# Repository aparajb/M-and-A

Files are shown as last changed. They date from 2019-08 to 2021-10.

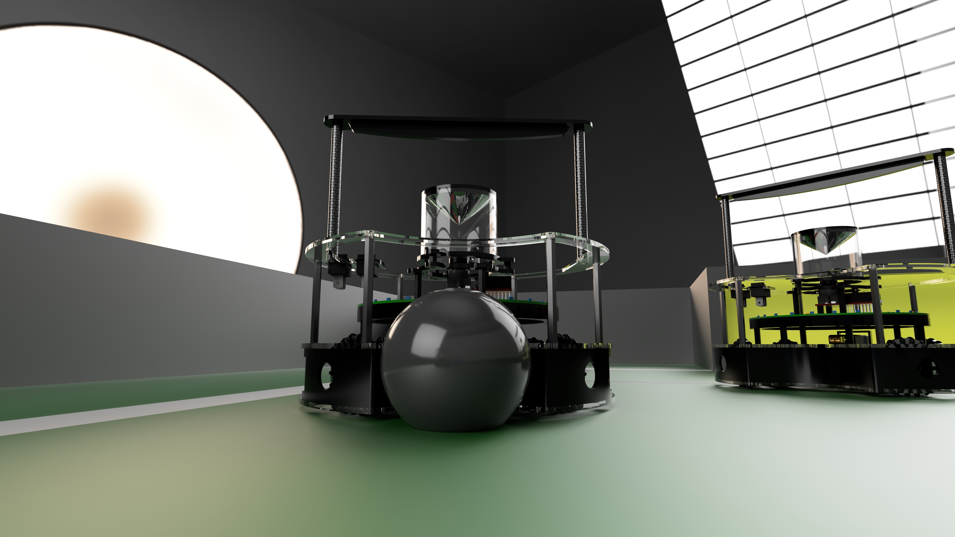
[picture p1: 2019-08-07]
M&A 2019/Hardware/Renders/Game Render 2.jpg

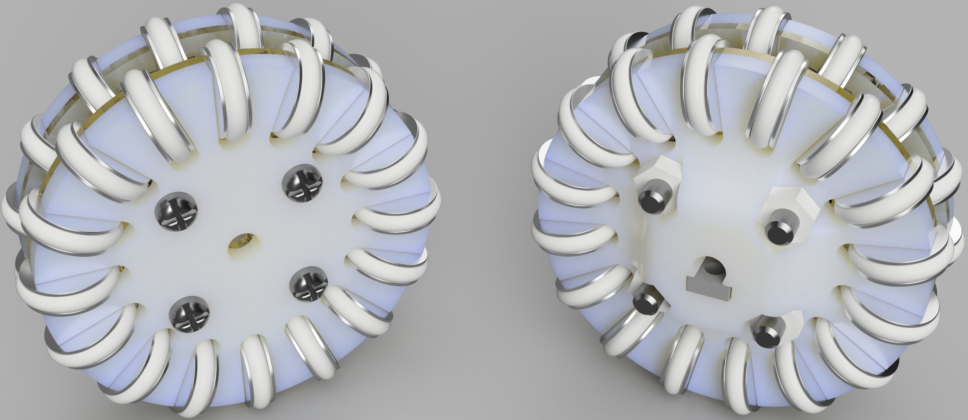
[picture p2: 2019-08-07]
M&A 2019/Hardware/Renders/Wheel.png

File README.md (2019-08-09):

# M&amp;A
#### M&amp;A Repository
**The Team:** Aparaj Bogahawatta, Matthew Feros, Gus Gannon
---------------------------------------------------------------------------------
**We are an Australian lightweight soccer team, competing in the Robocup Junior Lighweight League, as part of Brisbane Boys' College Robotics.**
For enquiries relating to BBC Robotics please visit:
[Brisbane Boys' College Website](http://www.bbc.qld.edu.au).

Alternatively, please contact the Head of Soccer at BBC: [Steven Lau](mailto:slau2@bbc.qld.edu.au).

For more information about Robocup Australia, please visit: [Robocup Junior Australia](https://www.robocupjunior.org.au/).

For more information about our Robots, please visit our website: [M&amp;A Robotics](https://bbcrobotics-mna.weebly.com).

## Folder Structure
- M&amp;A 2018 : All the designs, electronics and software for our 2018 national robots
    - Hardware : Contains all the structural components and electronic components of our robot
    - Log Book : Contains the manufacturing process of our original robot
    - Management : Contains some files for management
    - Orders : Contains an order spreadsheet which has all our electrical and structural components
    - Software : Contains the software for our microcontrollers
        - lib : Contains libraries of code referred to in the main program
        - src : Contains the source code for the Master Teensy

- M&amp;A 2019 : All the designs, electronics and software for our 2019 international robots
    - Documentation : Contains a handout, presentation and poster for our team.
    - Hardware : Contains all the structural components and electronic components of our robot
    - Orders : Contains an order spreadsheet which has all our electrical and structural components
    - Project Management : Contains our project management plan for the international competition
    - Rules : Contains the international and national rules    
    - Software : Contains the software for our microcontrollers
        - lib : Contains libraries of code referred to in the main program
        - src : Contains the source code for the Master Teensy
        
## Primary Robot Components
- Maxon DCX19s Motors
- Custom Made Omniwheels (3D Print, Laser Cut and CNC)
- Main PCB
    - Teensy 3.5
    - 24 TSSPs
    - IMU (MPU9250)
    - HC-05 Bluetooth Module
    - OpenMV H7
- Light Sensor PCB
    - 32 Light Sensors Arranged in a Circular Formation
- LRF PCB
    - 4 LRFs
- Custom Designed 360° Camera Mirror
## Programming Checklist
- [x] Establish Movement of Motors
- [x] Compass Correction
- [x] Ball Following + Score
- [x] Line Avoidance
- [x] Goal Tracking
- [x] Inter Robot Communication
## 2019 Objectives
#### General Goals
- [x] Increase Attacker accuracy
- [x] Increase Defender accuracy
- [x] Implement Role switching
## Results
#### Brisbane Regional Competition 2018
- 1st Place
#### Queensland State Competition 2018
- 1st Place
#### Australian National Competition Competition 2018
- 2nd Place
#### International Championships 2019
- 1st Place
---------------------------------------------------------------------------------



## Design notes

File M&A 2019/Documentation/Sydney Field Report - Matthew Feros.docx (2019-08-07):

Videos

https://www.youtube.com/channel/UCFLQQ7A4bBnele9LdO1RbSA/featured

Explain the interview process

There were three teams at a table, each table had 3 judges. A team would run through their presentation, which was shortened to 20 minutes max to 10. After the presentation, the judges would give the other teams a chance to ask you questions, and then the judges would ask question. Our judges only asked us one question, which was about our orbit function. I think we went well, considering we had to shorten our presentation in the moment.

Explain the poster marking process

Each team had to stand next to their poster and answer questions, mainly from other teams. There were 2 judges who walked around the posters, and I assume their marks were averaged at the end. They didn’t ask anyone questions about their posters.

Describe the quality of the referees

Most of the referees didn’t understand how pushing or multiple defence worked. In some cases they were completely biased with their calls, see this video https://youtu.be/-EMN1azKhEk?t=472. When they call multiple defence, they’re meant to call pushing at the same time and remove a robot and the ball from the goal box. In most cases, they would remove a robot from the box but leave the ball, and the other robot would score because of this sometimes. In some cases, they would remove the robot which had the ball, and count it as a goal. I think most of the referees were trainers of other teams. There was a small altercation with the rule about robots being pushed out in the finals. A referee saw our robot get pushed out by our other one, and they took it off. So we showed them the rule that says that any robot pushed out by any other robot may be put back in the field. So the referee’s played to the ‘may be’ part, and decided to only do the rule if it was opponent robots. The damage calls were very strict and sometimes unfair, the moment a referee saw the line pass the robot they would take it off for damage. They would only call pushing if it was happening in the goalie box.

Provide a copy of your full timetable/draw and results

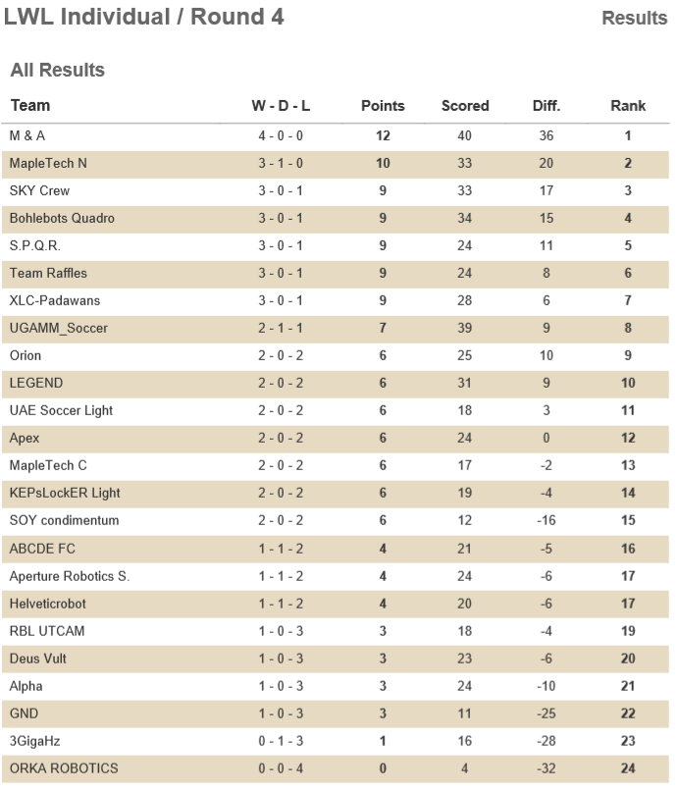
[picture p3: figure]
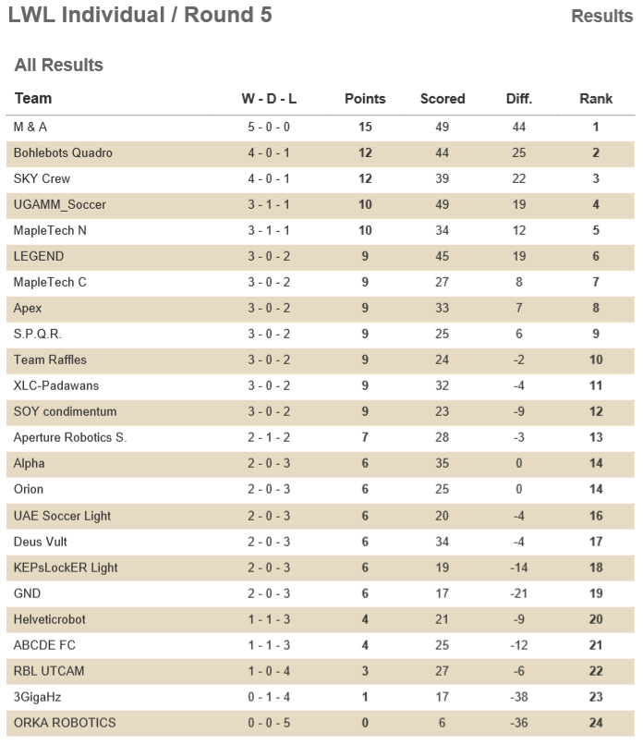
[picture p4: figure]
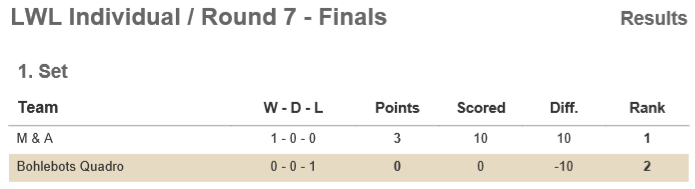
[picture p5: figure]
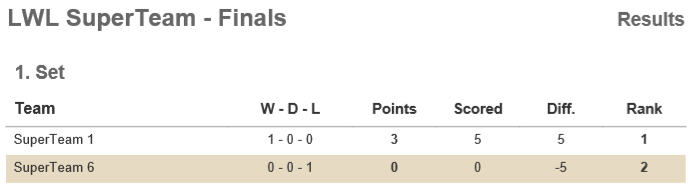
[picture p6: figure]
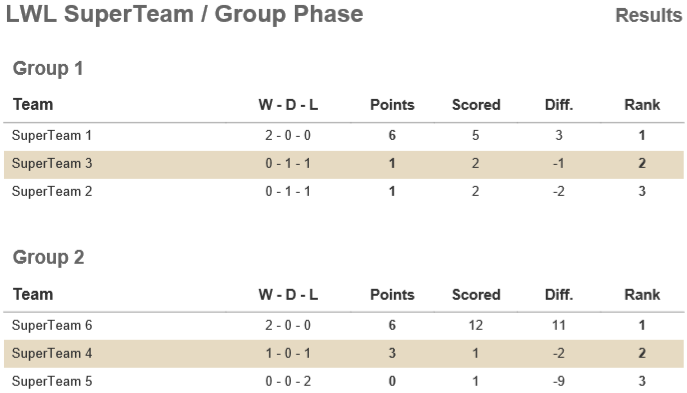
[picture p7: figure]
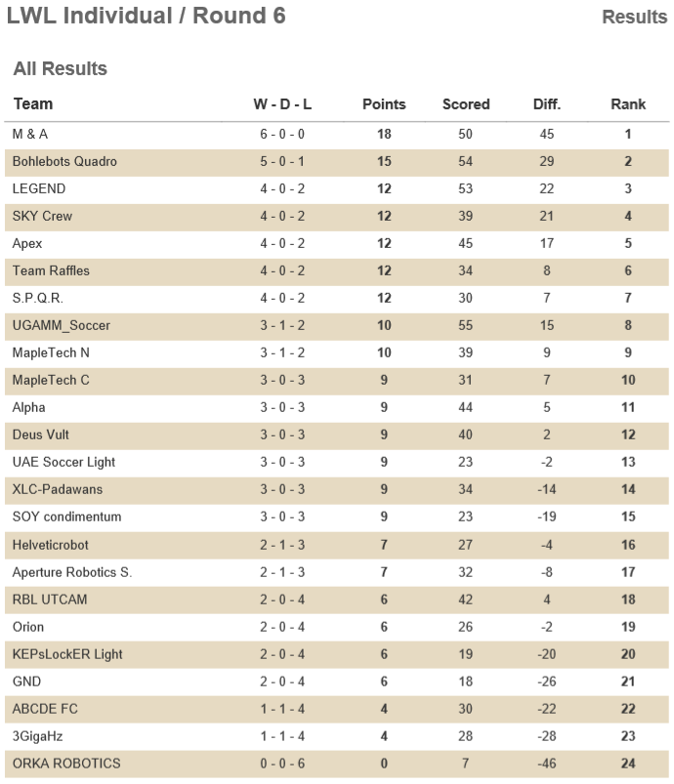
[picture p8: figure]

Describe the organisation of the event

The event was organised well, the games were on time and the fields were good (the goals were too short, at 80mm, which actually made it better for us.) The awards ceremony was not too good however.

Describe the inspection process and requirements

The inspection was fairly strict. I’m not sure if they had a rule on going 10 grams over the weight limit as this wasn’t an issue. They made you cover anything the same colour as the goal, no matter how small it was.

Describe your workspace

Our workspace was a large table with 4 chairs. It also had a power hub attached to it that had 4 power points, a usb port and usb-c port for charging. Our Superteam members weren’t seated near us, so we made a time to briefly meet and exchanged emails to talk that night. Our Superteam had teams from Israel, Singapore and Taiwan. Our superteam didn’t have any strategies. There was no Superteam interview. We beat all teams, however we had a very close match with Skycrew.

Intel on other teams

Skycrew along with some other teams employed aluminium plates approximately 1mm thick that were very lightweight and strong. Some teams also had lightweight solenoids. Bohlebots incorporated one that weight ~17 grams. They used 0.8mm wire wound around the body that was 30mm long, twice. They claimed that it would kick ¾ of the ramp, although I never saw it kick in game. Legend had a dribbler on their robot that consisted of a brushless motor and a roller bar. Their roller bar had not centre gap to centre the ball, and our robot would often hit the ball out quickly. They didn’t have any apparent strategy with it so I didn’t really get to see it in action. The dribbler can be seen in our game against LEGEND.

Our team’s strengths and weaknesses

We experienced very few issues. At the beginning of the competition our Open-MV began to power cycle because of an issue with the headers. This was fixed by hard-wiring its power into the voltage regulator. Aside from this, and having to tighten some bolts throughout the competition, our robots were very reliable. This was caused largely because of the lack of external wiring and strong construction after an emergency update to our top plate. We achieved our result because we had robots that were extremely consistent. Our goalie also meant that even with one robot off the field, we rarely had a goal scored against us. Our attackers tuning was also very effective when combined with the robot’s speed. This meant that our robots were at the ball first almost anywhere on the field.

Improvements for BBC

More production routes would definitely help in our robots quality. Being able to use materials such as aluminium and carbon fibre more freely would allow us to have more weight left over and have stronger robots. Extra weight would allow us to have more functionality in our robots, with things like dribblers, kickers and extra sensors. Taking some time to look into cheap routes of machining both carbon fiber and aluminium would be worthwhile for improving our robot’s performance. A kicker is used by some teams, most commonly in the form of a solenoid, however some teams used a motor with an arm on it to flick the ball. A kicker however probably wouldn’t help our robots be more effective, as they’re already fast, and a kicker only makes the ball move in a straight line which means that if the other team has a goalie it would be the same difficulty to stop. The ball would also likely slow down to the point where our robot would reach it again very quickly. For this reason, a lightweight team and some open teams use a dribbler which allows the robot to make different shot, possibly curving the ball into the goal, or driving to the goal backwards and turning quickly.

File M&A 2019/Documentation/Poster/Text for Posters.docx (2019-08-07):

# Abstract

M&A is an Australian team from Brisbane Boys’ College that have made two identical robots to compete in the RoboCup Junior Soccer Lightweight Competition. We consist of 4 team members. Last year we placed 1st at the Queensland State Competition and 2nd at the Australian National Competition. The robots have been developed since September of 2017 with four different design iterations for different RoboCup Competitions. We have worked for over 500 hours and spent approximately AUD$2500 on parts for the robot

The robots were built using industry technologies and incorporate populated Printed Circuit Boards (PCBs) to increase efficiency and reliability. The robots were programmed using the Arduino Framework. Each robot consists of two microcontrollers, a Teensy 3.5 and an OpenMV H7. The robots communicate via Bluetooth Modules to optimise gameplay performance.

The purpose of this poster is to share our findings on how to best build a robot for this competition so that other teams can improve their robots and to help RoboCup achieve their goal in making robots that can beat the best soccer players in the world by 2050.

# Robot Design and Production

~~Include a labelled diagram of the robot~~

## Overview

The structural design of the robot was created in Autodesk Fusion 360, and the PCBs were designed in Autodesk EAGLE. These programs were used since the different file types were compatible with each other, making it easier to visualise a finished robot and simulate the fit of components. Custom made parts, incorporated in the design, were either Laser Cut or 3D Printed. The PCBs were made at a fabrication service.

## Chassis Design

The robot is comprised of three separate layers which form the frame of the robot. This creates a robot which is easily accessible for both production, maintenance and repairs. The chassis is made up of three laser cut poly-carbonate plates.

- The bottom plate is designed to hold four DCX19 Maxon Motors, 32 LEDs and Phototransistors (Light Sensors) and a battery holder.
- The middle plate supports the Main PCB and provides additional support to the motors.
- The top plate is used to stop the robot from entering the goal area and protects the electrical components from accidental impacts.

The three plates are connected by lightweight nylon standoffs.

## Electrical Components

The robots’ electrical system is a combination of 3 printed circuit boards (PCB’s). PCBs were used in this robot to reduce the number of external connections, increasing the reliability of connection to different components. The PCBs are connected to each other by Flat Flex Connecters (FFCs) like ones used in many smartphones and tablets in the Tech-Industry. The PCB on the Bottom Plate (Light Sensor PCB) is used to detect the white line. The Light Sensor PCB holds:

- 5-bit Multiplexer
- 32 LEDs
- 32 Phototransistors

The PCB on the Middle Plate (Main PCB) holds all the main circuitry and the bulk of the components. It holds the two microcontrollers which calculates the robot’s movement. The Main PCB consists of:

- 1 Teensy 3.5 (Microcontroller)
- 1 OpenMV H7 (Microcontroller)
- 24 TSSPs (IR Sensors)
- 4 VNH5050A (Motor Controllers)
- 1 HC-05 (Bluetooth Module)
- 3.3V and 5V Power Supply for whole robot

## Laser Range Finders

The PCB above the cone is the LRF (Laser Range Finder) PCB. This PCB holds four Laser Range Finders which can detect the robot’s distance from the walls. There are mounted at the top of the robot so it can see over other robots. This array of 4 sensors allow the robot to have accurate positioning on the super team field and enhanced vision in regular game play.

## 360 Camera

# Software

Include Flow Chart of Robot Logic

## Overview

The robots have been programmed using C++ and Python with two microcontrollers on each robot. The Teensy 3.5 does the bulk of the calculations and receives data from all the sensors. The OpenMV H7 is an optical sensor that calculates the goal direction and distance and then sends those values to the Teensy. The Teensy then sends motor values to the motor controllers.

## Communication and Game Strategies

Each Robot has an HC-05 Bluetooth Module which pair with each other. The robots can send their role (Attacker or Defender), the ball direction and the ball strength (distance) using a Serial protocol. The robots can decide whether it should be an attacker or a defender and switch positions accordingly, just like real soccer players. This strategy is implemented in Gameplay and helps reduce the number of Double Defence fouls.

## Ball Following

Each robot has 24 digital IR sensors which output a value of 0, when it detects IR light, or 1, when it can’t detect IR light. The ball direction is calculated by using Vector Addition. After the ball direction is calculated, two mathematical models are used to calculate the move direction. The first one determines the angle added to the ball direction, so the robot positions itself behind the ball; the second one scales down the angle added based on how far away the ball is.

Include image of two functions.

## Out Avoidance

The robot incorporates 32 Light Sensors to detect the white line and stay in the field. The light sensors are arranged in a ring, makes it easier to perform vector calculations. The angle of the line is calculated using Vector Addition. This data is sent to the Teensy 3.5 and the robot moves in the opposite direction of the line, so it stays inbounds.

# Innovations

## Fusion of LRFs and Light Sensors to stay inbounds

The Software implemented on the robot uses a fusion of LRF and Light Sensor values to stay inbounds during gameplay. The LRFs can detect when the robot enters the edge of the playing field and slows down in this area. This is so the robot has a lower chance of going over the line.

## Bluetooth Position Strategies

The robots can play as two roles: Attacker or Defender. The robots utilise their Bluetooth connection to work out which robot is the Attacker or Defender and moves accordingly. If one of the robots is taken off the field, the other one will automatically become a defender.

## Vacuum Formed Mirrors

The mirrors on the robot were made using a mould and a vacuum and an oven to heat mirror material. The mirror material was first heated, then placed on a mould, where the material was vacuumed into the shape of the mould. This provide a smoother mirror surface which made it easier track the goal.

# Testing and Development

## Multidirectional Optical Vision Development

The optical vision system went through three main stages.

The first stage was a vertically mounted mirror in the shape of a ‘V’. This allowed a camera to look up into the mirror and see forwards and backwards.

Pros:

- The mirror could see the goal at great ranges
- Easy to manufacture

Cons:

- Small field of view in front and back directions, cannot see sideways

The second stage was a cone net that was wrapped around a 3D printed cone shape. This allowed the camera to have a 360-degree view.

Pros:

- Can see in all directions

Cons:

- Hard to manufacture
- View Distance is reduced
- Image distortion

The third stage was a vacuum formed convex mirror shape. The design process for this is explain in the Innovation section.

Pros:

- Can see in all directions
- Reduced Image distortion
- Easy to manufacture

Cons:

- View distance is reduced

The vacuum formed mirror was chosen for the robot as it was the most practical in gameplay and the pros of the mirror outweighed the cons.

## Wheel Development

An early iteration of this robot included the premade omni-wheels from GTF robotics. These were an easy to use omni-wheel, however they lacked in grip which caused the robot to slide as it attempted to avoid the line. The rubber O-rings included with the wheels also wore down very quickly and we couldn’t find any suitable replacement.

A new wheel was designed to fix this issue. It included larger rollers that were produced by a CNC lathe to have more grip on the floor, and the current iteration of this includes two layers to maximise contact with the floor. Include 3 photos of how wheels touch the ground.

## Electrical System Overhaul

## IR Sensor Ring

Wide slits in OG robot to just holes to holes that extend down.

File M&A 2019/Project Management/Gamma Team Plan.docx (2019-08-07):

# 2019 Custom Team Plan

You need to prepare a written plan for 2019 with your current team, until such time as your team changes. Please work on this document in Dropbox so the coaches can check as you go along. Note that this plan may be used as documentation for international teams.

## Report

Each team must prepare the following items in a single report. Your report should be as detailed as possible.

Section | Your report should cover: | Due Date for 1st Draft

Design overview

List of major parts, including what specific component you intend to use

Per Robot

- 3 Plates and handle
- 4 sets of GTF Wheels
- 4 Maxons
- 24 TSSPs
- 24 Light Sensors on PCB (multiplexed 24 sensors to 1)
- 1 IMU
- 1 Teensy 3.5
- 1 Pixy 2 / Open MV
- 1 Motor Controller PCB
- 1 Battery
- 1 Logic and TSSP mainboard PCB
- 24 Individual TSSP PCB’s
- 1 Power supply PCB
- 4 LRF’s
- LRF PCB on top of cone mirror

Robot structure and plate design

The robot will have a three plate design (3 plates and a handle for internationals to save weight). The light sensors, motors and motor controllers will be attached to the bottom plate. The battery will be stored between the middle and the bottom plate. The main PCB, TSSPs, IMU, Camera and Microcontroller will be secured on the middle plate. The top plate will hole our switches and handle (Handles will hold switches in ints robot).

Motor angles

45, 135, 225, 315

PCB plan

We will have one main PCB with all the components connected to it. This PCB will connect to the motors and sensors. It will be located in the centre of the robot so it is similar distance from all the sensors and motors.

Dribbler and kicker

We will aim to have a dribbler mounted at the front of the robot. It will be located inside the capture zone. This will result in a more reliable control of the ball.

Camera plan

We will have a cone mirror mounted above the camera. This will allow it to have a full 360 degree view. This will enable us to see both goals at the same time. This opens up opportunities for switching roles between attacker and defender.

Cartesian co-ordinate plan

We will use 4 distance measurement sensors on top of the 360 mirror to receive an exact x,y co-ordinate on the field. This will allow us to do some extra tactics to get past enemy goalies. This could also be used to allow the robots to avoid each other during a switch, potentially prioritising the path of the robot becoming an attacker or vice versa in different scenarios.

Materials

The materials we will be using are poly carbonate for the plates, some carbon fibre for the dribbler, carbon fibre rods with titanium nuts epoxied as standoffs, nylon nuts and bolts and metal nuts and bolts.

Wheels

We will use GTF wheels to allow full omnidirectional movement. This means that we are able to orbit the ball more efficiently and always face the direction of the goal.

Other

Thursday 18-Oct

Software plan

Changes and additional functionality to be made to 2018 software

We will develop Bluetooth communication between the robots to allow for in-game strategy. This means that we are able to have the robots switch roles during the game and always have a robot protecting the goal. In a game, there will be an attacker and a defender. If one robot gets taken off for damaged the Bluetooth modules will be disconnected. If this happens then the other robot will be told to become a defender if it isn’t already. Another way the Bluetooth will be useful, is when the defender has the ball in its capture zone, it will automatically become the attacker. This means that the attacker will become the defender, completing a ‘switch’. Another condition for a switch is if the attacker is behind the defender then it will become the defender and the other robot will become the attacker.

Another aim is to add a co-ordinate system of the field. This means that the robots will be able to be told a co-ordinate on the field and move to it. This means that if none of the robots can see the ball, it moves into a defensive formation to stop the other team from scoring a goal.

Code simplification and clean-up required

Not too much code simplification is required. This is because the code is very efficient and works reliably and accurately. Only fine tuning different PID values and orbiting values are required to make the robot even more accurate.

Other

We will also switch to using Visual Studio Code as a text editor rather than atom. We will also start to use the version controller Git so we are able to revert back to an older code if necessary.

I will also try and have as many functions that I can in libraries rather than the main.cpp. This means that all the code is more separated and spread throughout all the folders, rather than being in one file.

Thursday 18-Oct

R&D plan

Identify things that need further research

We need to research different types of distance sensors to use on our robots. We need to find a distance sensor that does not interfere with IR sensors and is accurate and reliable.

List items you would like to test and try – hardware and software

We would need to test the different types of distance sensors to make sure that they are accurate and do not interfere with IR sensors. We will need to test different types of cameras so we can find the fastest and most accurate camera. We would need to test the different types of dribbler rollers and see which one held the ball the best (this could be simplified by making all dribbler rollers fit the same assembly).

Thursday 18-Oct
Risk management | Identify the greatest risks to your project. What is most likely to fail? The thing that is most likely to fail is the main PCB. This is because it has most of the components of the robot and if one thing is slightly wrong, the whole robot will break. Identify steps you will take to manage these risks and make your robots more reliable To fix this issue we will need to make everything as simple as possible and even consider moving some of the components of the main PCB and onto other, smaller PCBs. | Thursday 18-Oct
LW to Open Transition Plan (team TBC) | Explain how you will modify or rebuild LW international robots in time for states and nationals. We wouldn’t really need to rebuild the robot to transition into open. All we would need to do is rebuild the mirror and remove the TSSPs. For the software side, the ball angle calculations would change. This is because the camera is only used to calculate the ball direction. This will mean that a more accurate co-ordinate system will be required because the robot will not always see the ball. | Thursday 25-Oct

## Project Management Plan

Each team must create a project management plan. This can be done in either GanttProject or with the existing Excel Task Management sheet.

Section | Your plan should cover: | Due Date

Project management plan

Job allocation – leave this blank until teams are announced

We would try and split the jobs in the team to software, testing, design, hardware and electronic. We would try and split the work load evenly between the team members.

Create a project timeline

1. We need to make a list of all the parts that we will definitely be using on our robots and make sure that there are enough of them for us to use. If not we will need to order them before the end of term 4.
2. We then have to design the robot and the electronics before the end of 2018.
3. We will then order all the parts that we haven’t already ordered at the start of 2019.
4. After our parts arrive, we will aim to have the robot built by the middle of March, preferably middle of February.
5. This leaves us over two months to test the robot and to solve and hardware or software issues that may arise.

Monday 22-Oct

## Draft Parts List

Section | Explanation | Due Date

Parts list with cost and weight estimates

Complete a parts list using the 2019 order sheet template. A weight estimate should be included, including for Open div. and except for maze

- Handle
  - Switches (Button switches)
- Middle Plate
  - Logic Board
    - Connectors (Flat Flex Ribbon cable)
      - Light sensor
      - TSSP’s
      - Quad distance sensors
      - Motor controller
    - Camera (Pixy 2 / Open MV)
    - Micro-controller (Teensy 3.5)
    - IMU (MPU9250)
    - Bluetooth module (HC05)
  - TSSP PCB x 24
    - TSSP (TSSP 58038)
    - Connector (Flat Flex Ribbon cable)
- Base Plate
  - Base Plate PCB
    - 4 x Motor controllers (probably VNH7100BASTR)
    - Connector (Flat Flex Ribbon cable)
    - 24 LED’s
    - 24 Light Dependant Transistors
      - Multiplexer to convert 24 sensors to 1 analogue port
    - Connector (Flat Flex Ribbon cable)
  - 4 x Maxon DCX 19 12V 16:1

You decide this in your project management plan

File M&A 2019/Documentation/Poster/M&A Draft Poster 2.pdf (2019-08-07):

M&A

Method, Production & Design | Abstract | Data, Results & Discussion

# Hardware Overview

# Chassis Design

# Electrical Components

# Software Overview

# Communication & Game Strategies

# Ball Following

# Out Avoidance

# Camera

# Wheels

# LRFs

# Vacuum Formed Mirrors

M&A is an Australian team from Brisbane Boys’ College. Our team of four have have made two identical robots to compete in the RoboCup Junior Soccer Lightweight Competition. Last year we placed 1st at the Queensland State Competition and 2nd at the Australian National Competition. The robots have been developed since September of 2017 with five different design iterations for

different RoboCup Competitions.

## We have worked for over 500 hours and spent approximately AUD$2500 on

parts for the current robot.

## The robots were built using industry technologies and incorporate Printed Circuit Boards (PCBs) to increase efficiency and reliability. Our robots also incoporate LRFs to track the robot’s position on the field. The robots

communicate via Bluetooth Modules to optimise gameplay performance.

## This poster shares our findings on how to best build a robot for this competition so that other teams can improve their robots. This will Whelp RoboCup achieve their goal in making robots that can beat the best soccer players in the world by

2050.

# TEAM PICTURE

The structural design of the robot was created in Autodesk Fusion 360, and the PCBs were designed in Autodesk EAGLE. These programs were used since the different file types were compatible with each other, making it easier to visualise a finished robot and simulate the fit of components. Custom made parts, incorporated in the design, were either Laser Cut or 3D Printed. The PCBs designed by us and ordered from a fabrication service.

The robot is comprised of three separate layers which form the frame of the robot. This creates a robot which is easily accessible for both production, maintenance and repairs. The chassis is made up of three laser cut poly-carbonate plates.
- The bottom plate is designed to hold four DCX19 Maxon Motors, 32 LEDs and Phototransistors (Light Sensors) and a battery holder.
- The middle plate supports the Main PCB and provides additional support to the motors.
- The top plate is used to stop the robot from entering the goal area and protects the electrical components from accidental impacts.
The three plates are connected by lightweight nylon standoffs.

The robots’ electrical system is a combination of 3 printed circuit boards (PCB’s). PCBs were used in this robot to reduce the number of external connections, increasing the reliability of connection to different components. The PCBs are connected to each other by Flat Flex Connecters (FFCs) like ones used in many smartphones and tablets in the Tech-Industry. The PCB on the Bottom Plate (Light Sensor PCB) is used to detect the white line. The Light Sensor PCB holds:
- 5-bit Multiplexer
- 32 LEDs
- 32 Phototransistors
The PCB on the Middle Plate (Main PCB) holds all the main circuitry and the bulk of the components. It holds the two microcontrollers which calculates the robot’s movement. The Main PCB consists of:
- 1 Teensy 3.5 (Microcontroller)
- 1 OpenMV H7 Camera (Microcontroller)
- 24 TSSPs (IR Sensors)
- 4 VNH5050A (Motor Controllers)
- 1 HC-05 (Bluetooth Module)
- 3.3V and 5V Power Supply for whole robot

The robots have been programmed using C++ and Python with two microcontrollers on each robot. The Teensy 3.5 does the bulk of the calculations and receives data from all the sensors. The OpenMV H7 is an optical sensor that calculates the goal direction and distance and then sends those values to the Teensy. The Teensy then sends motor values to the motor controllers.

Each Robot has an HC-05 Bluetooth Module which pair with each other. The robots can send their role (Attacker or Defender), the ball direction and the ball strength (distance) using a Serial protocol. The robots can decide whether it should be an attacker or a defender and switch positions accordingly, just like real soccer players. This strategy is implemented in Gameplay and helps reduce the number of Double Defence fouls.

Each robot has 24 digital IR sensors which output a value of 0, when it detects IR light, or 1, when it can’t detect IR light. The ball direction is calculated by using Vector Addition. After the ball direction is calculated, two mathematical models are used to calculat`e the move direction. The first one determines the angle added to the ball direction, so the robot positions itself behind the ball; the second one scales down the angle added based on how far away the ball is.

The robot incorporates 32 Light Sensors to detect the white line and stay in the field. The light sensors are arranged in a ring, makes it easier to perform vector calculations. The angle of the line is calculated using Vector Addition. This data is sent to the Teensy 3.5 and the robot moves in the opposite direction of the line, so it stays inbounds.

The 360-degree camera vision system is comprised of the Open MV H7, a custom moulded mirror and acrylic tube. The mirror is shaped as a cone and is vacuum formed over an impression to create a detailed mould. The camera is positioned so that it looks vertically at the cone, then through the mirror on the cone can see the entire field. A series of brackets allow the cone to be positioned to the centre of the camera’s field of view. A circular piece of card is placed above the cone to protect the camera from glare which would wash out the image.

Pros:
- The mirror could see the goal at great ranges
- Easy to manufacture
Cons:
- Cannot see sideways
- Image Distortion
- Worse for Gameplay

Pros:
- Can see in all directions
- Reduced Image distortion
- Better for Gameplay
Cons:
- View distance is reduced
- Harder to manufacture

Side on View of the robot
V Mirror Render | Cone Mirror Render
Pixel Distance | Pixel Distance

Actual Distance (cm)
Actual Distance (cm)

Graphs of the relationship between the Pixel Distance and the Actal Distance for both mirrors

An early iteration of this robot included the premade omni-wheels from GTF robotics. These were an easy to use omni-wheel, however they lacked in grip which caused the robot to slide as it attempted to avoid the line. The rubber O-rings included with the wheels also wore down very quickly and we couldn’t find any suitable replacement.

A new wheel was designed to fix this issue. It included larger rollers that were produced by a CNC lathe to have more grip on the floor, and the current iteration of this includes two layers to maximise contact with the floor.

# QR CODE

Orbit Function | Ball Distance Scale

The Software implemented on the robot uses a fusion of LRF and Light Sensor values to stay inbounds during gameplay. The LRFs can detect when the robot enters the edge of the playing field and slows down in this area. This is so the robot has a lower chance of going over the line.

The mirrors on the robot were made by using a mould, vacuum and an oven to heat and mould the mirror material. The mirror material was first heated, then placed on a mould, where the material was vacuumed into the shape of the mould. This provide a smoother mirror surface which made it easier track the goal.

Robot Logic Flowchart

LRFs Avoidance Coordinates

The LRFs send data
to the Teensy 3.5 via
a Serial protocol. It
sends 16-bit values
and has millimetre
accuracy.

Slow Area

Slow Area

Normal Area

Wheel Progression - GTF Wheel, Single Layered Custom Wheel, Double Layered Custom Wheel (Left to Right)

Main PCB

Light Sensor PCB

LRF PCB

BRISBANE BOYS’ COLLEGE
JUNIOR LIGHTWEIGHT SOCCER
Current Ball Angle (o) | Proportional Ball Strength

Ball Angle Offset

Relative Ball Distance

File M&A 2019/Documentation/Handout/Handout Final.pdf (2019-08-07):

# M&A MORE INFORMATION

Brisbane Boys’ College, Australia

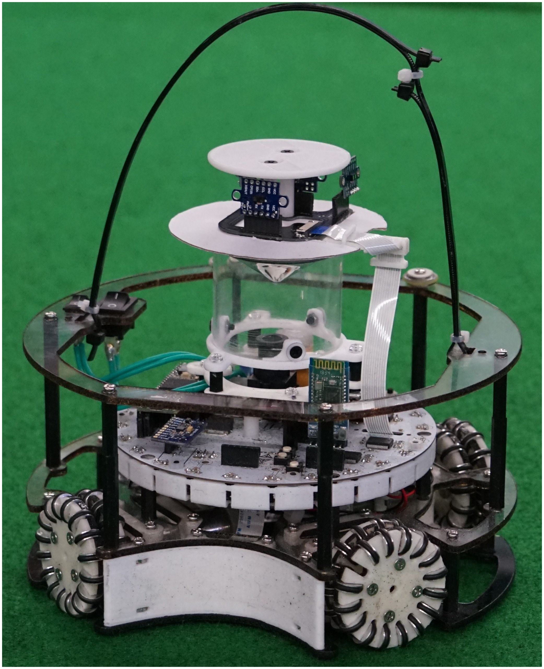
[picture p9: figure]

For more information feel free to visit our website, bbcrobotics-mna.weebly.com or use the QR code below. Also see our poster or talk to one of us in person for more information, we are more than happy to share our knowledge.

Matthew Feros - 18440@bbc.qld.edu.au

Gus Gannon - 90311@bbc.qld.edu.au

Aparaj Bogahawatta - 24989@bbc.qld.edu.au

Taehwan Kim - 23648@bbc.qld.edu.au

THE TEAM | INNOVATIONS

## Advanced Line Avoidance

The Laser Range Finders (LRFs) give the robot a distance to the wall with millimetre accuracy. These distances are used to know the robot’s position on the field. This means that we can tell if the robot is near the line and pre-emptively slow down before we touch the line. This decreases the amount of times the robot goes out of the field and is called off for damaged. If the robot does go on the line, the light sensors will detect and avoid the line.

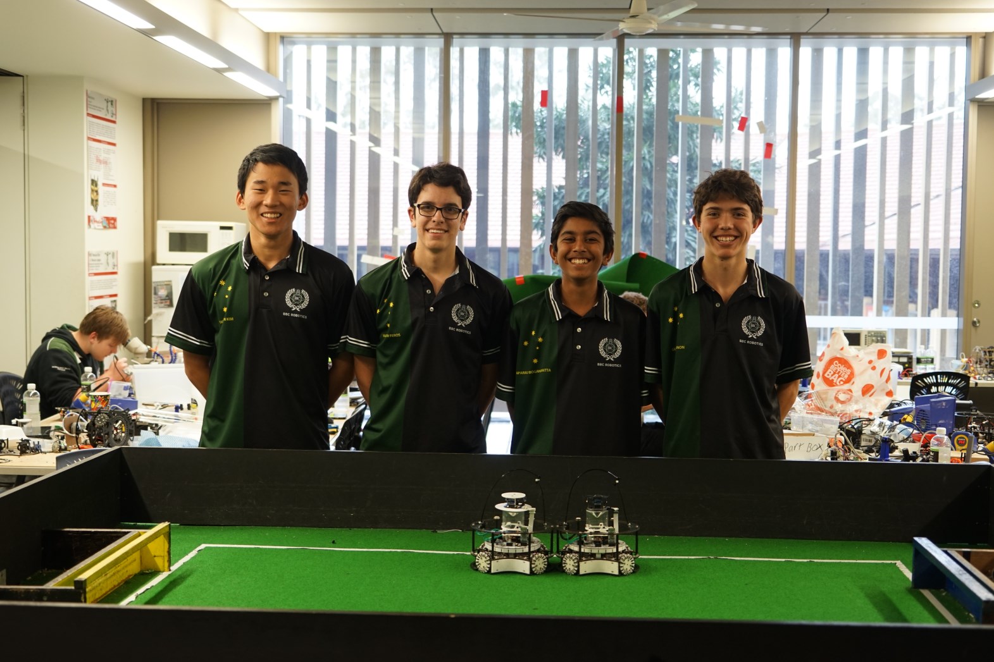
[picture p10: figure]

The LRFs will also aid in goal

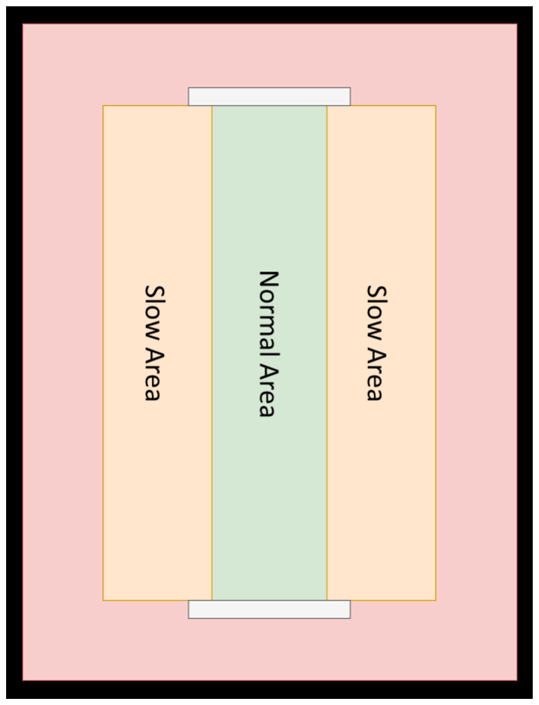
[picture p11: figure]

tracking in the Super-team
scenario as the large field size makes it harder for the camera to track the goal. This is because the field’s size is larger than the camera’s view range.

M&A is an Australian team from Brisbane Boys’ College competing in the Robocup Junior Lightweight Soccer division. Our team of four have made two identical robots to compete. Last year we placed 2nd at the Australian National Competition. The robots have been developed since September 2017 with five different design iterations for different RoboCup Competitions. Our team consists of four members (left to right): Taehwan Kim, Matthew Feros, Aparaj Bogahawatta and Gus Gannon.

ROBOT SOFTWARE | ROBOT HARDWARE
| Robot Structure The robot is comprised of three separate layers which form the frame of the robot. This creates a robot which is easily accessible for both production, maintenance and repairs. The chassis is made up of three custom-made laser cut poly-carbonate plates. The three plates are connected by a combination of lightweight nylon and metal standoffs. These are used in conjunction with 3D printed custom parts to form the structure of our robot. Our robot also has a convex, cone-shaped mirror that was custom made by vacuum forming mirror material to a custom-designed 3D printed mould. This allows the vertically facing camera to have a full 360 degree field of view. The 3D models for the components of our robot were made in the software Autodesk Fusion 360 and were printed using respective team member’s 3D printers.

## Ball Following

Each robot has 24 digital IR sensors with an output value of 0 when it detects IR light, or an output value of 1 when it can’t detect IR light. We calculate the ball angle and distance by using the top four values and using vector addition. After the direction of the ball is calculated, two mathematical models calculate where the robot should move. The first model determines the angle added to the ball direction, so the robot positions itself behind the ball (orbit function); the second model scales down the angle added based on how far away the ball is (distance scale function).

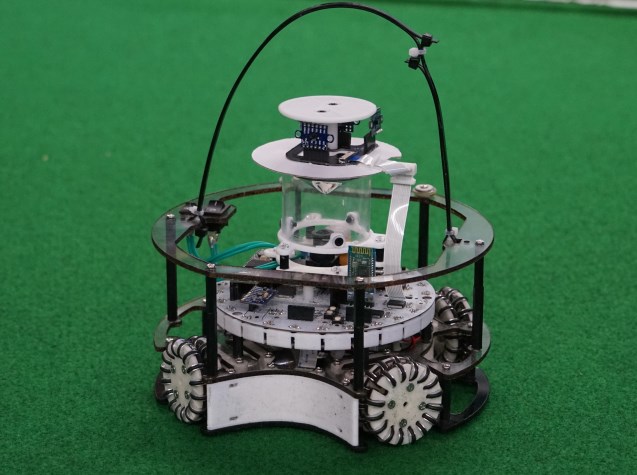
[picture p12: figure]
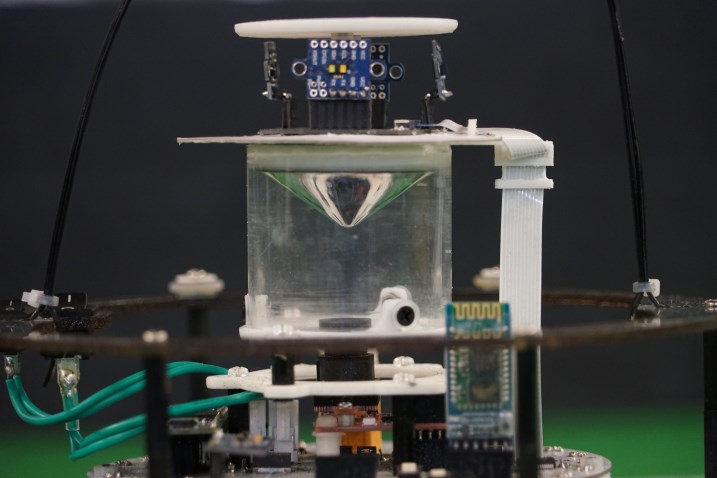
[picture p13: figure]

M&A Robot | M&A 360 degree mirror

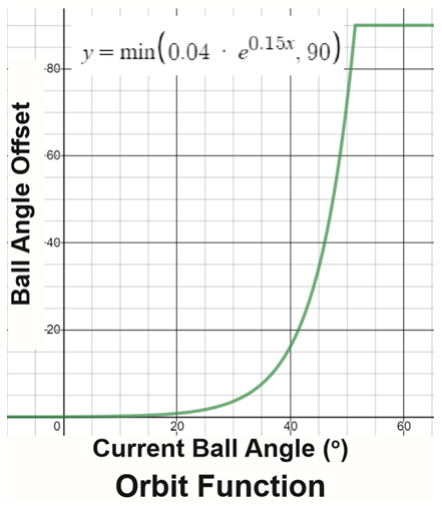
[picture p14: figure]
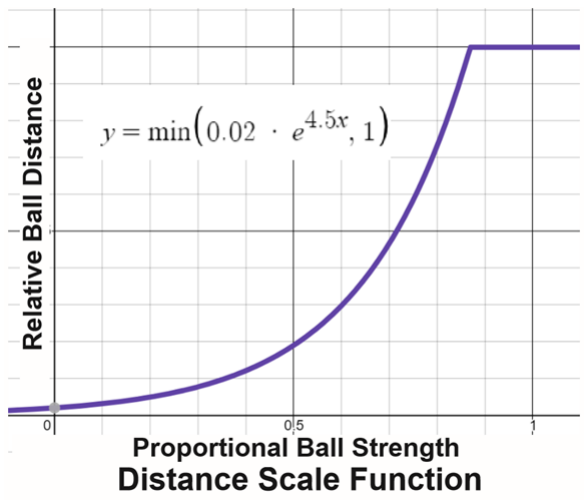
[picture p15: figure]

ROBOT HARDWARE | ROBOT SOFTWARE

## Electronics

The robots’ electrical system is a combination of 3 custom-made printed circuit boards (PCB’s) designed in the software Autodesk Eagle. PCBs were used in this robot to reduce the number of external connections, increasing the reliability of connection to different components. The PCBs are connected to each other by Flat Flex Connectors (FFCs) like ones used in many smartphones and tablets in the Tech-Industry. The PCB on the Bottom Plate (Light Sensor PCB) is used to detect the white line. The PCB on the Middle Plate (Main PCB) holds all the main circuitry and the bulk of the components. It holds the two micro-controllers which calculate the robot’s movement. The middle plate also houses the Bluetooth modules that enable the robots to communicate with each other. This is used to switch the robot’s role between attacker and defender mid game.

## Overall Logic

The robots have been programmed using C++ and Python with two micro-controllers on each robot. The Teensy 3.5 does the bulk of the calculations and receives data from all the sensors. The OpenMV H7 is an optical sensor that calculates the goal direction and distance and sends those values to the Teensy. The Teensy then sends motor values to the motor controllers. The robot follows a set of steps, shown in the Robot Logic Flowchart, to determine where it should move.

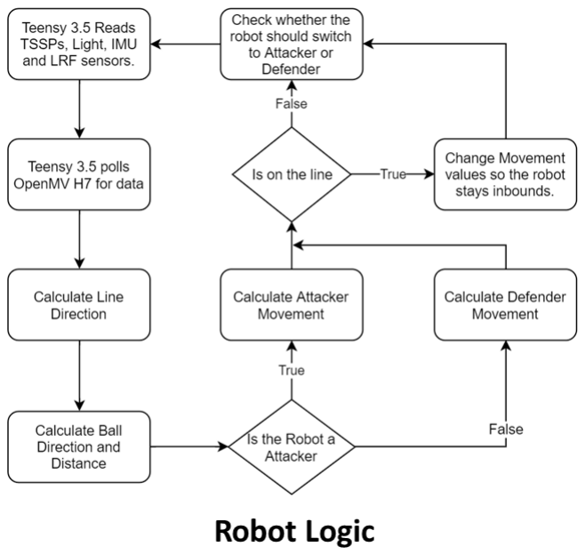
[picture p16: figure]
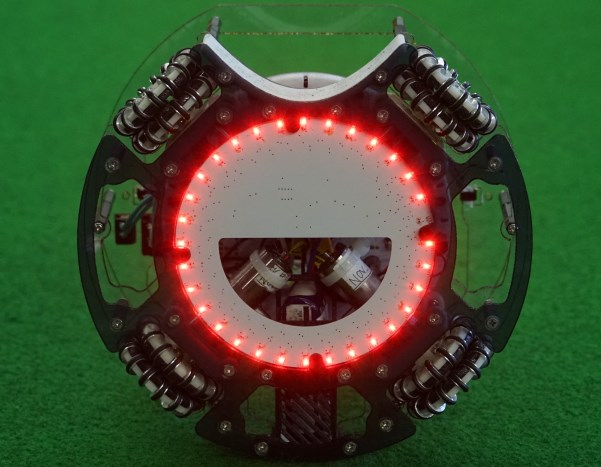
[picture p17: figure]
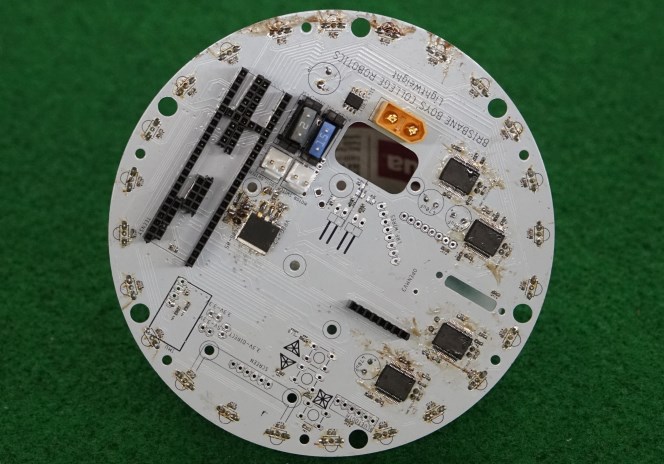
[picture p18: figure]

M&A light sensor PCB | M&A main PCB

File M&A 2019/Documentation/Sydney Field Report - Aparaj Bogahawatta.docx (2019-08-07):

# Field Report - Aparaj

RoboCup 2019 was hosted by Australia and the competition was an amazing experience. The Major and Junior Leagues were all held in the International Convention Centre (ICC) in Sydney. There was a variety of countries that competed with a various ethical and cultural backgrounds. The exceptional organisation and the excellent equipment led to a high-quality competition.

# Videos

All our games can be found on YouTube by searching M&A robotics or clicking the following link https://www.youtube.com/channel/UCFLQQ7A4bBnele9LdO1RbSA.

# Interview

The interviewing process this year was different to previous processes. The 20-minute individual interview was replaced with a 40-minute group interview. Each group consisted of three individual teams. The teams were allocated 10 minutes to present their robots to the group. The remaining 10 minutes was used as a question and answer period after each team’s presentation. Our group consisted of a Mexican team and an Italian Team.

The new format presented a challenge for our team since we had prepared for a 20-minute interview. We had created a PowerPoint presentation that was designed to last 20-minutes. In order to stay within the time constraints, we had to skip over some of our slides. This did not present much of a problem since the timing for our 20-minute presentation had included a question and answer period. In our question and answer period none of the other teams asked us any questions. The only person to ask us a question was the main interviewer, Marek Suppa. He asked us how we calculated the movement for our robot. This was answered easily since it was a relatively simple question.

There were four interviewers that interviewed the group. Marek asked all the questions and was the most interactive interviewer. This was because he was the only interviewer that could speak English easily and fluently. He seemed to be more interested in the software components of our robots and how our software was constructed.

I believe that our interview went very well as the new time factor didn’t really affect us too much. We were able to cover all the important aspects of our robots but still go into enough detail so others knew how our robots worked and the manufacturing process of our robots. I believe that this new process has benefits and detriments. The main benefit is we can share our ideas and processes to other teams in our group and we are able to ask and answer questions. The main detriment is that we couldn’t go into as much detail as possible, meaning we couldn’t explain all our innovative features. In my opinion the new process is better since it is easier for interviewers to compare different teams which is advantageous towards us.

# Poster

The posters were marked in a 2-hour poster presentation session. All the teams from the same league would stand next to their poster and explain their robots to anyone who was interested. This encouraged teams to go around and talk to other teams about their robots and share ideas to better improve their robots in the future. Our poster had a lot of visitors since we were currently in first place.

There was a marker that came around looking at all the posters. The marking criteria for the poster which is found on the international marking rubrics. The marker would sometimes ask questions, but this was very rare. Even though there was a marker, the main purpose of the session was to share ideas to other people and to interact with people from all over the world. This process was very effective as everyone who was competing in our league was able to interact with other people from around the world.

# Point Weightings

On-Field Performance – 40%

Interview – 10%

Poster – 20%

Teamwork – 10%

Team Spirit – 10%

Tech Challenges – 5%

Portfolio – 5%

# Referees

All the referees were volunteers or mentors. This meant that many of them did not know all the rules or misinterpreted certain rules. This didn’t really affect our team as we normally played on the top tables which consisted of the confident referees who understood all the rules. Most of the referees understood the basic rules, so the majority of gameplay was able to run smoothly. The main discrepancy in refereeing was the pushing rule. Most of the referees did not understand the pushing rule and this led to some wrong calls. This meant that most of the goals against us was technically pushing and some of the goals for us was also technically pushing.

Unlike the previous years, the double defence rule was not as strict as the years before. This is because most of the referees were not as familiar with the rules. However, in comparison to the Australian refereeing the double defence call was much stricter. If the referee knew the double defence rule, they would only call double defence when an opposing robot was pushing the other two robots into the penalty area. This meant that most of the double defence calls were useless as two robots were already in the penalty area when the attacker was trying to score. The damage call in relation to double defence was never used in any of the games since the referees were unaware of this rule.

The out of bounds rule was very strict at internationals. As soon as the robot went out it was taken off, even if it was trying to come back in. This presented a problem due to the speed of our robots. Since our robots were so fast, the referees would think that our robot had gone out even though it hadn’t. This meant that our robot sometimes got taken off for damaged even though it should have stayed in play. The pushed-out call presented a problem for us since our robots still tried to re-enter the field if the referees picked it up. We were able to overcome this problem since the referees were open to us explaining our robot logic in relation to our line-over logic.

# Results

Throughout the competition we did not lose a single game. Our results can be found at https://drive.google.com/drive/folders/16U67NBvkr9AkMXo2WcytCHHbYLBjVjl4. The marking rubric for all the aspects of the poster, presentation and teamwork can be found on the RoboCup Junior website.

# Event Organisation

The competition was organised very well. All the information in relation to game times was on a board just outside the competitor work area. This meant that we could easily find out when and what field our games were. Open and Lightweight games were at different times, so the fields weren’t too crowded. There were only two testing fields which meant that it was normally very crowded. This didn’t really present a problem for us as we didn’t really test too often. The inspection area was in between the fields and the work area so it was very easy to access. The fields were spread out so there was enough space for the referees, competitors and spectators. The layout of the fields was very effective and used the space well.

# Inspection Process

The inspection process was very rigorous. All the limitations of robots were checked. The size, weight, capture zone, handle and batteries on the robot were all tested. In addition, the colour and LEDs on our robots were tested to make sure they didn’t interfere. This meant that inspection did take a while but the people inspecting our robots were very quick and efficient. As well as the normal inspection at the start of the day, there were random inspections throughout the competition. We only had one random inspection which had no hiccups. This inspection process is a lot stricter than the inspections in local competitions.

# Workspace

The work area allocated to us was very small and inadequate. Each team got one table with four chairs. The table was very small, and we could barely fit all our components on the table. As a result, we ended up keeping most of our tools in our toolbox. We only took them out when we needed them. We also kept our robots in their boxes rather than on the table just so we could save space. The table was also equipped with four power points (daisy-chaining was banned). We didn’t end up using all the power points since our computers were always fully charged and we only needed power point to charge our batteries. We did need to keep all our gear organised, so we didn’t take up other teams’ space. Sometimes our neighbouring teams would take up part of our area due to their small work area. This didn’t present an issue as we had two great teams next to us. The work area was very poor, but we were able to overcome this problem by keeping our gear organised.

# SuperTeam

The SuperTeam competition is where multiple teams are combined into different SuperTeams. These teams then play a game of soccer on a field that is 4 times larger than a normal field. Each SuperTeam is allowed 5 robots on the field at a time, and each individual team needs to have at least one robot. Our SuperTeam consisted of GND (Israel), Team Raffles (Singapore) and SOY condimentum (Taiwan). We were able to have both our robots on the field because there were only four individual teams in our SuperTeam.

There were six SuperTeams and they were separated into two groups. There were two games where each team would play the other two teams in their group. The top team in each group would then play in the final. This process was fair in determining the best team but was not as good as determining second and third place. This didn’t matter since only first place was acknowledged with an award.

Our Superteam decided that we should have one defender and four attackers. This was so we didn’t let any goals in but had good attacking power. We decided to do this because goals in a SuperTeam game are a lot rarer, so we needed as many attacking robots as possible. At first Team Raffles used their robot as a defender but they had some issues with their compass so their defender couldn’t work. We ended up using our defender since it was the best defender and it ended up working well. We didn’t employ many game strategies since we weren’t able to calculate our position of the field due to its size. The SuperTeam competition was a way for all the competitors to have fun and to enjoy the competition.

SuperTeams did not have an interview but the way we worked together was a part of the Teamwork marks.

# Competitors

Our performance against other teams was very successful. The only teams that caused a problem was the two Japanese teams. This is due to the accuracy and speed of their robots. This was complemented by the strong hardware design which allowed their robots to be reliable.

Sky Crew had a very well-built robot with no top plate. They were able to fit all their components in a very small space. Their robots were very accurate, and their defender was very effective. This was due to their effective software. They also had line over detection which enabled them to go on the other side of the line and get the ball. They did not implement this in our game since they ran their robots at a higher speed. The main downside of their robots was the speed of their robot. This meant that their robot was not able to score as many goals since it wasn’t able to get to the ball first. When they did get the ball, their robots did not move that fast, except they had a very powerful kicker that made it difficult to defend against. Their defender, however, was very accurate and was able to stop almost all the goals that other robots might try and score against them. The only goal that we were able to score against them was when their defender crashed and moved away from the goal. This is a testament to the quality of their goalie.

Team LEGEND had the best robots in the whole competition; however, due to bad luck their compass sensors broke. Unfortunately, they did not have any spares, meaning their defender was useless; however, when their robots were working, they were very fast and very accurate. Their attacker had a dribbler and a kicker, which they used to bypass goalies effectively. They implemented strategies where they could attempt to hide the ball from the goalie and then quickly move back and shoot. The also could turn and shoot simultaneously so the goalies weren’t able to respond in time. Their defender only had a very wide capture zone, with a kicker. Their defender was broken for most of the competition, but it looked like it just moved in front of the goal. We were able to beat them because they only had their attacker on the field. Their defender was off for the whole game. This meant that whenever the ball was behind their robot, we were able to score.

# Self-Evaluation

## Weaknesses

The main weakness of the robot was the reliability of components on the PCB. We found that due to the speed of the robots, some of the components on the PCB would fall out. This was easily fixed with hot glue. Another weakness of our robot was its inability to score against teams with strong defenders. The game against Sky Crew was very intense and close since none of the attacking robots could score against the opposing defender. The best way to fix this issue is to incorporate a dribbler and a kicker into next year’s robots, but to maintain the reliability of our current robots. Another weakness was the construction of the wheels. The double layered wheels were effective; however, the O-rings were very thin and did not have much contact with the carpet. The best way to fix this is to have thicker O-rings, even if that means we would have less rollers all together. By having thicker O-rings, there will be increased contact with the ground, meaning that the robot can change directions faster.

## Strengths

The main strength of our robots was its speed, accuracy and reliability. Our robots were one of the fastest robots, the most accurate and reliable robots in the whole competition. These factors helped us achieve the results that we did. Since our defender was very effective, we did not let many goals in. This meant that it was very difficult for teams to beat us due to the quality of our defender.

# Improvements and R&D

I believe that BBC needs to invest in making our components as space efficient as possible. I think that the space between the bottom and middle plate needs to be used more effectively so we can have more components but not need more space. We also need to invest in making a better dribbler and a lighter kicker so we can implement more game strategies.

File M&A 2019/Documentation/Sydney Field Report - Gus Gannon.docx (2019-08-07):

Gus Gannon Robocup 2019 Sydney field report

Interview

During the interview three teams were taken to a small booth and each was given just under ten minutes to give a presentation about their robots. After each presentation, the other teams got the chance to ask questions before the adjudicators asked. After this, the next team presented and so-on until all three teams had presented. Neither of the other teams asked us any questions and only one of four adjudicators asked a single question. This interviewer was Marek Suppa (Robocup Committee member) and his question was asking how Aparaj found the constants in his orbit calculation. I believe that our interview presented in an informative way given that the other teams and the adjudicators did not feel the need to ask questions at the end. Something that I may have done differently is give handouts to all members present and direct them to certain sections of the handout as we speak, as well as using our slides.

Poster

The poster marking process was not as competitor involved as I expected it to be. The adjudicators came around, looked at our poster and moved on. No questions were asked. Members and mentors of other teams, however, used this time to ask us questions about our robot which kept us busy for the full duration of time allocated for the poster session.

Weightings

The performance in gameplay was worth 40%. The poster was worth 20% and the interview was worth 10%. 10% was given to teamwork which was marked at random, unknown times throughout the competition. 5% was awarded for team spirit as voted by other teams, 5% for signing up for the technical challenges, 5% for filling out a form prior to the commencement of competition.

Referees

Most of the referees were either university students or team mentors that needed to fill in time. They often were strict enough with the out of bounds rule however, on occasions, there were some inconsistencies. Firstly, if the referee wasn’t paying attention to a certain robot and it went out, they often wouldn’t question teams on whether it was pushed out or not and just agreed with whatever the team said. Another inconsistency came from referee to referee. Some interpreted the “pushed out rule” as the robot would not be pulled off as damaged if it was pushed out regardless of team and others took a robot off if it was pushed out by its own teammate. Each interpretation was kept consistent throughout the entire match, however. The “pushing” calls were not as frequent as I expected from watching videos of last year’s competition. Pushing was still called when it was obvious that a robot had been moved however, there were some cases where a robot may have been touched by another robot and pushing was not called, which is a violation of the rules. The calling of multiple defence was a weak point for the referees. Many would not call the rule unless reminded by the teams present. The selection of which robot to move was also not equal as some referees removed the robot causing the least effect on the current situation and others would remove the robot that was blocking the goal, ending with some conceded goals that were unfair. The pushing rule was much looser in superteam games and was often interpreted differently by referees manning opposite goals on the same field. Clarification of the pushing rule to teams and referees needs to be carried out before next year’s competition. Another issue with the refereeing during the superteam matches was the referees handling the ball on the field not being agile enough and blocking or even stepping on robots. This could be solved by giving them opaque gloves that block IR light, stopping all robots on the field when they move the ball. This was also an issue during individual games. Referees were often too slow to move the ball from neutral point to neutral point, ending with our robots already taking up the neutral point in question. This caused a passing back and forth between referees that went on for several seconds. This was avoided in some matches when the referees used opaque gloves.

Results

We won individual and superteam (ytb)

Organisation

The event was overall well-organised. Game schedules and results were posted well in advance of the next round of games. Referees were mostly punctual to the matches and the organising committee were open to questions and were easy to access throughout the competition. There were two main issues in organisation throughout the competition. The crossbar being two centimetres short was one such issue. This was dealt with well by the even organisers, however, there was much fighting on the teams’ part to get to the result. The abundance of blue light around the fields was the other issue. Even if the screen had a white image on it, the blue light projected would interfere with goal-tracking. This could be solved by not having RGB LEDs of any description near the playing area.

Inspection

The inspection test was like the Australian domestic competition. They used a flat board with a 3D printed hemisphere that was used to test the capture zone depth. They also used a set of electronic scales to measure the weight of the robot and a cylinder like the one in our room to test robot size. Then then used a multimeter to test battery voltages and made us turn the robots on to check for LEDs.

Workspace

The workspace was one table, about the size of those found in the middle school, with four chairs around it and a power board. These were pre-assigned.

Superteam

The superteam competition had four countries play five robots on a larger field with normal rules. We shared a superteam with the Israeli’s (GND), Taiwanese (SOY compendium), and Singapore (Raffles). We were the team that sported two robots in this competition, and we won. We used our attacker and defender; the rest of the team used their attackers. There was no superteam interview and comments about refereeing have been stated earlier.

Competitors

We went undefeated throughout the competition however, there were two teams that were very close to us. SkyCrew was one of these teams. They had very similar robots to ours and we only managed to win 1-0. The main difference was their use of crosshair light sensors instead of a circle. Legend were another good team who, in my opinion, had the best robots on the field when they were working however, their robots were often breaking and for most of our game against them they only had one robot. They managed to fit both a kicker and dribbler on their robot which is something we aim to have at next-year’s competition. The main weakness for most teams was reliability. Most teams had broken robots at some stage in the competition which is one of the reasons why I believe our team and the German team (Bohlebots Quadro) were so successful.

Self-evaluation

I think a weakness I had was that I would move around the venue looking at other exhibitions without informing the rest of my team where I went. I think that I worked well in that I managed to stay calm during tense moments and could think about situations strategically. This was important as being the ‘team captain’ meant that I was the one who could speak with the referees. I think this was done effectively. I believe that we achieved the results we did because we set deadlines for different sections of the robot very early which gave us more time to weed out issues. The reliability of our robots also contributed to our success.

Improvements for BBC

What we need to do in the future is be more prepared in the future. R&D needs to be completed well in advance of competition in order for an adequate amount of testing time is to be carried out. The quality of the robots is also not necessarily the most important part. We found that in games it wasn’t always the team with the best robots that won, but the team with the most consistent robots. Team Legend for example in our league probably had the best robots when they worked however, they were often breaking, ending with them getting fourth in gameplay. There aren’t many advanced strategies in lightweight which is an opportunity for BBC to take the lead. There are some strategies that I have theorised that will need to be tested however, these require both a kicker and dribbler which our robots currently don’t have.

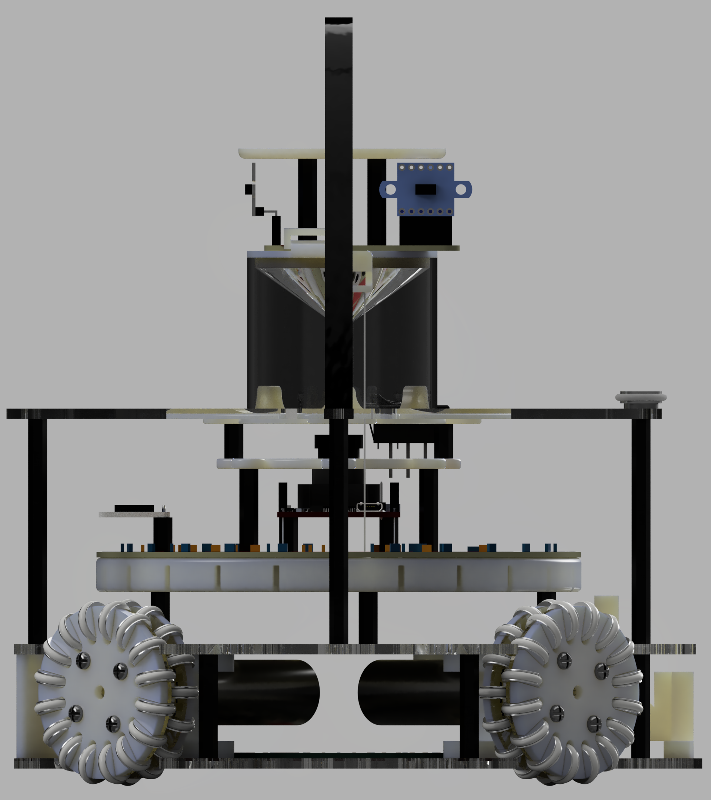
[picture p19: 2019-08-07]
M&A 2019/Hardware/Renders/Layer Display.png

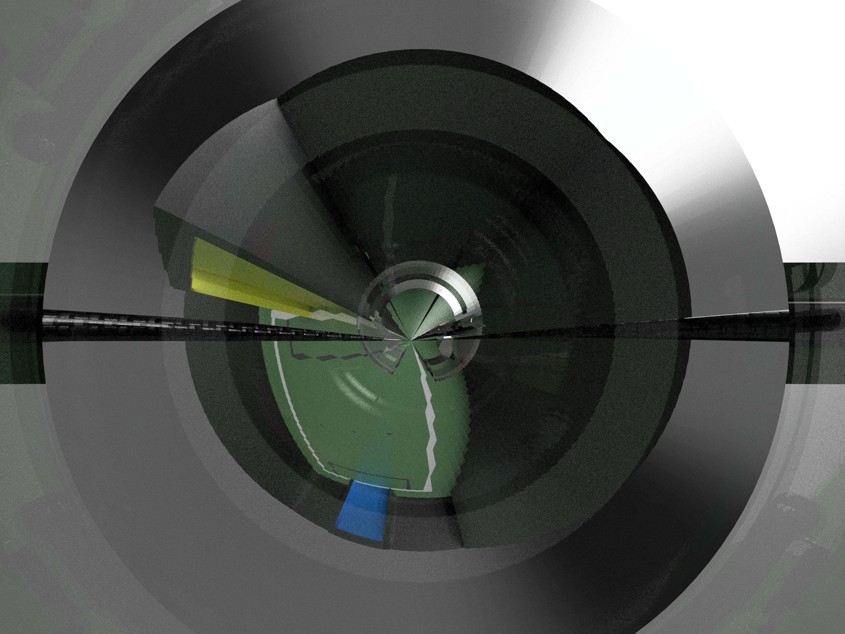
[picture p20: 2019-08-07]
M&A 2019/Hardware/Renders/Mirror Render 2.jpg

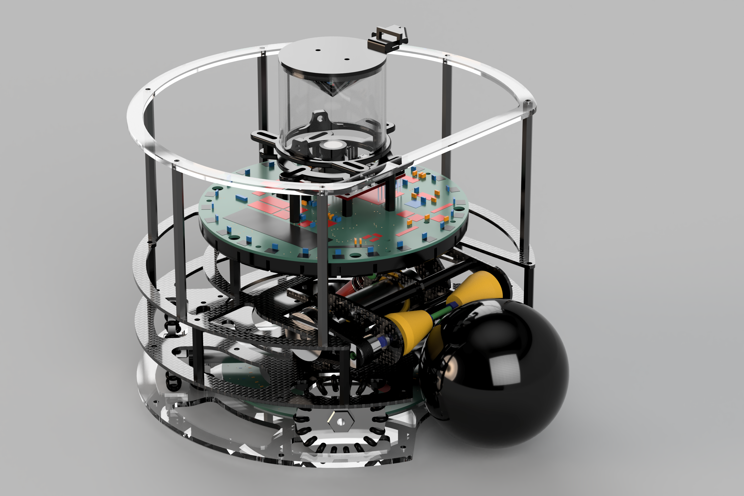
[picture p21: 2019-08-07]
M&A 2019/Hardware/Renders/Dribbler Robot.png

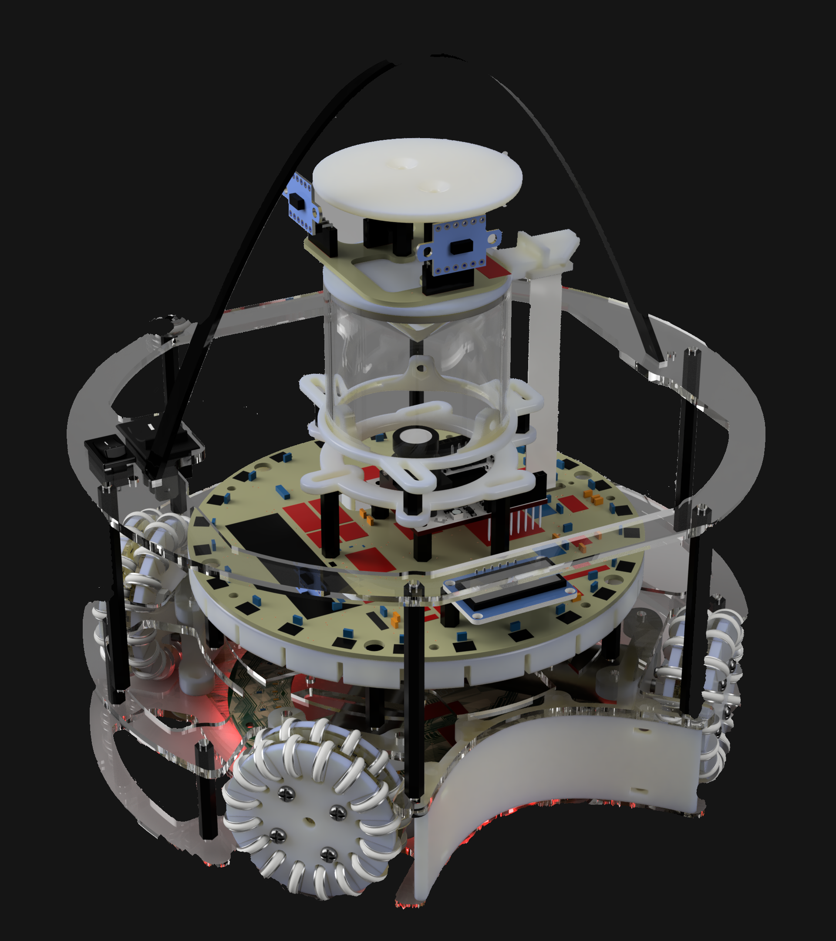
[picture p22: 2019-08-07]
M&A 2019/Hardware/Renders/Portrait Render - Dark.png

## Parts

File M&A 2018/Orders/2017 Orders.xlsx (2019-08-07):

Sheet: Parts Template
Date Submitted | Team | Item | Description | Supplier | Vendor PN | Total QTY (inc. spares) | Spares | Price per unit in original currency | Original Currency | Total price (AUD) | Link | Notes
2017-01-01 | TSR | Cap | 1uF 0603 10% | Little Bird |  | 1 | 0 | 0 | AUD | $0.00 | www.bbc.qld.edu.au | Example only
2017-01-01 | TSR | Resistor | 100K 0805 1% | Digi-Key |  | 1 | 0 | 0 | AUD | $0.00 | www.bbc.qld.edu.au | Example only
2017-01-01 | Shared | 12vie | Basically everyone | BBC |  | 1 | 0 | 0 | AUD | $0.00 | www.bbc.qld.edu.au | Example only
2017-01-01 | TSR | Screw | M3 10mm | Digi-Key |  | 1 | 0 | 0 | AUD | $0.00 | www.bbc.qld.edu.au | Example only
2017-01-01 | TSR | Order 66 | Emperor Palpatine | Clones |  | 1 | 0 | 0 | USD | $0.00 | www.bbc.qld.edu.au | Example only
2017-01-01 | TSR | Converter | Power Converters | Tosche Station |  | 1 | 0 | 0 | USD | $0.00 | www.bbc.qld.edu.au | Example only
2017-01-01 | TSR | Xpeliamus | Magic Wand | Diagon Alley |  | 1 | 0 | 0 | USD | $0.00 | www.bbc.qld.edu.au | Example only
2017-01-01 | TSR | Motivator | R2-3P0 Hyperdrive | Falcon Freight |  | 1 | 0 | 0 | USD | $0.00 | www.bbc.qld.edu.au | Example only
2017-01-01 | TSR | Swag | Cool kid | Steven |  | 9001 | 1 | 9001 | CRED | $0.00 | www.bbc.qld.edu.au | Example only
2017-01-01 | TSR | Parkour lessons | 007 | Steven |  | 9001 | 1 | 9001 | CRED | $0.00 | www.bbc.qld.edu.au | Example only
2017-01-01 | TSR | Cabinet | Magic | Room of requirement |  | 1 | 0 | 0 | AUD | $0.00 | www.bbc.qld.edu.au | Example only
2017-01-01 | TSR | Cap | Adjustable strap | Uniform shop |  | 1 | 0 | 0 | AUD | $0.00 | www.bbc.qld.edu.au | Example only
2017-01-01 | TSR | Resistor | Resistor | The Resistance Base |  | 1 | 0 | 0 | AUD | $0.00 | www.bbc.qld.edu.au | Example only
2017-01-01 | TSR | Kylo | Ben | HAN |  | 1 | 0 | 0 | AUD | $0.00 | www.bbc.qld.edu.au | Example only
2017-01-01 | TSR | Platypus | Secret agent | Disney |  | 1 | 0 | 0 | EUR | $0.00 | www.bbc.qld.edu.au | Example only
2017-01-01 | TSR | Tardis | Blue | Gallifrey |  | 1 | 0 | 0 | AUD | $0.00 | www.bbc.qld.edu.au | Example only
2017-01-01 | TSR | Sponge | Supremely idiotic | Bikini Bottom (Pineapple) |  | 9 | 10 | 21 | AUD | $0.00 | www.bbc.qld.edu.au | Example only
2017-01-01 | TSR | Starfish | Supremely idiotic | Bikini Bottom (Rock) |  | 9 | 10 | 21 | AUD | $0.00 | www.bbc.qld.edu.au | Example only
2017-01-01 | TSR | Werewolf | Page 394 | Professor Snape |  | 394 | 0 | 0 | GBP | $0.00 | www.bbc.qld.edu.au | Example only
2017-01-01 | TSR | Win | 1st place | BBC |  | 1 | 0 | 0 | AUD | $0.00 | www.bbc.qld.edu.au | Example only
2017-01-01 | TSR | Excel | Slightly humorous spreadsheet, even though spreadsheets are the most boring thing in the entire world. I honestly can't believe you bothered reading this. You can stop reading now. | Steven |  | 1 | 0 | 0 | AUD | $0.00 | www.bbc.qld.edu.au | Example only
2017-01-01 | TSR | Earth | The whole thing | God Himself |  | 1 | 0 | 5000000000000000 | USD | $7020000000000000 | www.bbc.qld.edu.au | This is real
2017-01-01 | Shared | 555 timer | Diamond encrusted | Rolex |  | 1 | 0 | 9999 | AUD | $9999.00 | www.bbc.qld.edu.au | Example only
2017-01-01 | LJ STAND | Mixtape | Secret | wallo |  | 1 | 0 | 9001 | CRED | $0.00 | www.bbc.qld.edu.au | Example only
2017-01-01 | LJ STAND | Snake | It's not a snake | wallo |  | 0 | 0 | 0 | AUD | $0.00 | www.bbc.qld.edu.au | Example only
2017-01-01 | Shared | Spirit | College | BBC |  | 1 | 0 | 0 | AUD | $0.00 | www.bbc.qld.edu.au | Example only
2016-09-18 | LJ STAND | Picture | Borrowed from the Qantas museum | wallo |  | 1 | 0 | 0 | AUD | $0.00 | www.bbc.qld.edu.au | Example only
2016-09-17 | LJ STAND | 7/11 | Prank call | wallo |  | 1 | 0 | 0 | AUD | $0.00 | www.bbc.qld.edu.au | Example only
2016-10-10 | FG & B | Bottle flip | Broken glass | Hulbert |  | 1 | 0 | 0 | AUD | $0.00 | www.bbc.qld.edu.au | Example only
2017-01-01 | LJ STAND | Price | Weight | Tudor |  | 1 | 0 | 0 | AUD | $0.00 | www.bbc.qld.edu.au | Example only
Ongoing | Shared | Ban petition | #StandWithNakul | some 12vies |  | 1 | 0 | 0 | AUD | $0.00 | www.bbc.qld.edu.au | Example only
2016-09-16 | Shared | Roll away beds | Broken and dangerous | Sydney hotel |  | 1 | 0 | 0 | AUD | $0.00 | www.bbc.qld.edu.au | Example only
2017-01-01 | Shared | Hot chocolate | Freshly made | Andrew |  | 1 | 0 | 0 | AUD | $0.00 | www.bbc.qld.edu.au | Example only
2017-10-20 | Shared | Slack banter day | Annual | some 12vies |  | 1 | 0 | 0 | AUD | $0.00 | www.bbc.qld.edu.au | Example only
2016-09-18 | LJ STAND | Broken Mega | Death by Harambe | Team Harambe 2016 |  | 1 | 0 | 0 | AUD | $0.00 | www.bbc.qld.edu.au | Example only
2016-09-18 | FG & B | Candle | Flame on | Motor controller |  | 1 | 0 | 0 | AUD | $0.00 | www.bbc.qld.edu.au | Example only
2016-10-27 | Shared | Nerf war | All out | Hulbert |  | 1 | 0 | 0 | AUD | $0.00 | www.bbc.qld.edu.au | Example only
2017-01-01 | LJ STAND | Scissors | Don't run with them | Doshi |  | 1 | 0 | 0 | AUD | $0.00 | www.bbc.qld.edu.au | Example only
2002-01-01 | Shared | BBC Robotics | It's pretty fun | His Greatness Mr Noy |  | 1 | 0 | 0 | AUD | $0.00 | www.bbc.qld.edu.au | Example only
 | Shared | Caravan Park | Nationals 2015 | Adelaide

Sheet: ORDERS
Order # | Date Submitted | Team | Item | Description | Supplier | Vendor PN | Total QTY (inc. spares) | Spares | Price per unit in original currency | Original Currency | Total price (AUD) | Link | Notes | Approval | Notes | Status | Purchase date | ETA | Actual Arrival Date | Purchased by | Shipping/ Other Costs | Grand Total / Actual Total Cost
145 | 2016-12-05 | New custom teams | Motor | 25mm diameter 500rpm | AliExpress |  | 20 | 3 | 11.43 | AUD | 206.10 | https://www.aliexpress.com/item/DC-12V-500RPM-25GA-40mA-High-Torque-Electric-Gear-Box-Motor-25MM/32270478250.html | Including shipping | Approved |  | Delivered | 2016-12-07 | 20-41 days | ~18/12/2016 | Steven |  | $193.97
146 | 2016-12-05 | New custom teams | Motor mount |  | AliExpress |  | 24 | 4 | 1.2 | AUD | 30.82 | https://www.aliexpress.com/item/Aluminium-alloy-25mm-25GB-GA-gear-motor-Bracket-with-Matching-screw/32660288599.html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 | Including shipping | Approved |  | Delivered | 2016-12-06 | 26-51days |  | Steven |  | $30.82
147 | 2016-12-05 | New custom teams | Motor controller | L298n dual | AliExpress |  | 16 | 4 | 2.01 | AUD | 45.13 | https://www.aliexpress.com/item/Free-shipping-1pcs-lot-Special-promotions-2pcs-lot-L298N-motor-driver-board-module-stepper-motor-smart/1872427142.html | Including shipping | Approved |  | Delivered | 2016-12-06 | 24-49days | 2017-01-04 | Steven |  | $45.13
148 | 2016-12-05 | New custom teams | Microcontroller | Arduino Mega | Ebay |  | 7 | 3 | 10.39 | AUD | 72.73 | http://www.ebay.com.au/itm/Mega-2560-R3-REV3-ATmega2560-16AU-Board-USB-Cable-Compatible-For-Arduino-HC-/252279621232 |  | Approved |  | Delivered | 2016-12-06 | Fri. 23 Dec. and Mon. 13 Feb. | late Jan 2017 | Steven |  | $72.73
149 | 2016-12-05 | New custom teams | 3D printing |  | Andrew |  | 0 |  | 0 | AUD | 0.00 | [3D printing] | TBC | Approved |  | In progress |  |  |  | Andrew |  | $0.00
150 | 2016-12-05 | New custom teams | TSOP ring |  | Andrew |  | 1 | 1 | 0 | AUD | 0.00 | [3D printing] | The TSOP ring will be 3d printed and form a middle plate that is elevated from the bottom plate using standoffs just like this year. | Approved |  | In progress |  |  |  | Andrew |  | $0.00
151 | 2016-12-05 | New custom teams | TSOPs |  | Tris10 |  | 2 | 28 | NA | NA | 120.00 | https://tris10.com/product/ir-sensor-50 | Will be ordered collectively for all teams | Approved |  | Delivered | 2016-12-23 |  |  | Tristan |  | $120.00
152 | 2016-12-05 | New custom teams | Wheels |  |  |  | 0 | 0 | NA | NA | 0.00 |  | Already in stock | Approved |  | In stock |  |  |  | ----- |  | $0.00
153 | 2016-12-05 | New custom teams | LDR | 50pcs | Ebay |  | 1 |  |  |  | 2.43 | http://www.ebay.com.au/itm/50pcs-Photo-Light-Sensitive-Resistor-GL5528-Photoresistor-Photocell-LDR-5mm-/291568788812 |  | Approved |  | Arrived | 2016-12-06 | Fri. 23 Dec. and Wed. 18 Jan. | 2016-12-30 | Steven |  | $2.43
154 | 2016-12-05 | New custom teams | LED | 5mm Red 100pcs | Ebay |  | 1 |  | 1.05 | AUD | 1.05 | http://www.ebay.com.au/itm/281632283748 |  | Approved | Link changed. Previous item could take as long as February to be delivered. | Arrived | 2016-12-06 | Thu. 22 Dec. and Tue. 17 Jan. | late Dec 2016 | Steven | $0.79 | $1.84
155 | 2016-12-05 | New custom teams | IMU | MPU9250 | AliExpress |  | 10 | 4 | 4.62 | AUD | 46.20 | https://www.aliexpress.com/item/MPU-9250-GY-9250-9-axis-sensor-module-I2C-SPI-Communications-Thriaxis-gyroscope-accelerometer-triaxial-magnetic/1904077579.html | This is basically your compass sensor | Approved | More expensive than last year. Not sure why | Delivered | 2016-10-13 | 24-49days | January | Steven | $2.88 | $49.08
156 | 2016-12-05 | New custom teams | Battery | Turnigy 1000mAh 3S | HobbyKing |  | 12 | 0 | 15.34 | AUD | 184.08 | https://hobbyking.com/en_us/turnigy-nano-tech-1000mah-3s-25-50c-lipo-pack.html |  | Approved |  | Delivered | 2017-02-05 | 3-10 days |  | Steven |  | $184.08
157 | 2016-12-05 | New custom teams | Battery Charger | Turnigy TQ4 4x6s | HobbyKing |  | 1 | 0 | 96.47 | AUD | 96.47 | https://hobbyking.com/en_us/turnigy-4x6s-lithium-polymer-battery-pack-charger.html |  | Approved |  | Delivered | 2017-02-05 | 3-10 days |  | Steven |  | $96.47
158 | 2016-12-05 | New custom teams | Power Supply | Turnigy Reaktor Pro 350W 23A Power Supply (100~240V AC) | HobbyKing |  | 1 | 0 | 72.33 | AUD | 72.33 | https://hobbyking.com/en_us/turnigy-reaktor-pro-350w-23a-power-supply-100-240v-ac.html |  | Approved |  | Delivered | 2017-02-05 | 3-10 days |  | Steven |  | $72.33
159 | 2016-12-05 | New custom teams | Power Cable | IEC C5 1.8m | Jaycar |  | 2 |  | 6.95 | AUD | 13.90 | https://www.jaycar.com.au/3pin-mains-plug-to-iec-c5-clover-leaf-1-8m/p/PS4120 |  | Denied | Wrong plug? |  |  |  |  | ----- |  | $0.00
160 | 2016-12-05 | New custom teams | Lipo Bags |  |  |  | 0 |  |  |  | 0.00 |  |  | Approved | Enough stock | N/A |  |  |  | ----- |  | $0.00
161 | 2016-12-05 | New custom teams | Veroboard | 40pc pack | Banggood |  | 2 | 0 | 14.07 | AUD | 28.14 | http://www.banggood.com/40Pcs-FR-4-Double-Side-Prototype-PCB-Printed-Circuit-Board-p-995732.html |  | Combined with other order | See #75 |  |  |  |  | ----- |  | $0.00
162 | 2016-12-05 | New custom teams | Wheel Hubs | Pololu Universal Aluminum Mounting Hub for 4mm Shaft, #4-40 Holes | Pololu |  | 10 | 1 | 6.12 | USD | 81.70 | https://www.pololu.com/product/1997 | Pack of 2 | Approved |  | Delivered | 2017-01-24 |  | 2017-02-01 | Steven |  | $81.70
163 | 2016-12-05 | New custom teams | Jumper Wires | 20cm, F-F, M-F, M-M | AliExpress |  | 2 |  | 4.12 | AUD | 8.24 | https://www.aliexpress.com/item/free-shipping-Dupont-line-120pcs-20cm-male-to-male-male-to-female-and-female-to-female/32668758951.html |  | Approved |  | Delivered | 2016-12-06 | 23-45days | 2016-12-30 | Steven |  | $8.24
164 | 2016-12-05 | New custom teams | Jumper Wires | 10cm, F-F, M-F, M-M | AliExpress |  | 2 |  | 2.66 | AUD | 5.32 | https://www.aliexpress.com/item/Dupont-line-120pcs-10cm-male-to-male-male-to-female-and-female-to-female-jumper/32328010671.html |  | Approved |  | Delivered | 2016-12-06 | 23-47days | 2016-12-30 | Steven |  | $5.32
165 | 2016-12-05 | New custom teams | Fuse | 2A 20pcs | AliExpress |  | 2 |  | 1.37 | AUD | 2.74 | https://www.aliexpress.com/item/20Pcs-Lot-2A-ATM-Mini-Blade-Fuse-Assortment-Auto-Car-Motorcycle-SUV-FUSES/32683738472.html | TELL SELLER YOU WANT 2A | Approved | TELL SELLER YOU WANT 2A. Order increased from 1 to 2 | Delivered | 2016-12-06 | 23-47days | late Dec 2016 | Steven |  | $2.74
166 | 2016-12-05 | New custom teams | Fuse | 7.5A 50pcs | AliExpress |  | 1 |  | 3 | AUD | 3.00 | https://www.aliexpress.com/item/High-Quality-50pcs-New-Car-Auto-Truck-Mini-Blade-Small-7-5A-Fuses-VE402-P/32751599689.html |  | Approved |  | Delivered | 2016-12-06 | 23-45days | 2016-12-01 | Steven |  | $3.00
167 | 2016-12-05 | New custom teams | Diode | 10A 45V Shottky | DigiKey | SR1045-TPMSCT-ND | 10 | 4 | 0.91 | AUD | 9.10 | http://www.digikey.com.au/product-detail/en/micro-commercial-co/SR1045-TP/SR1045-TPMSCT-ND/2334476 |  | Approved |  | Delivered | 2016-12-23 |  |  | Tristan |  | $9.10
168 | 2016-12-05 | New custom teams | Fuse Holder | MINI Fuse Holder, vertical, 50 pack | AliExpress |  | 1 |  | 26.72 | AUD | 26.60 | https://www.aliexpress.com/item/SL-1538-MINI-Style-Blade-Fuse-Holers-PCB-Mount-Fuse-holders-0153008/503553051.html |  | Approved |  | Delivered | 2016-12-06 | 24-49days | ~20/12/2016 | Steven |  | $26.60
169 | 2016-12-05 | New custom teams | Voltage Regulator | LM7805 2A 5V | DigiKey | 497-1468-5-ND | 10 | 4 | 0.819 | AUD | 8.19 | http://www.digikey.com.au/product-detail/en/stmicroelectronics/L78S05CV/497-1468-5-ND/585989 |  | Approved |  | Delivered | 2016-12-23 |  |  | Tristan |  | $8.19
170 | 2016-12-05 | New custom teams | Switch | Red Toggle Switch 4pcs | AliExpress |  | 1 |  | 3.88 | AUD | 3.88 | https://www.aliexpress.com/item/DC12V-20A-Indicator-Panel-Mounting-ON-OFF-Car-Toggle-Switch-Red-green-yellow-blue/32397900424.html | CHOOSE RED | Approved | CHOOSE RED. Order reduced from 2 to 1. Pack of 4. | Arrived | 2016-12-06 | 23-45days | 2016-12-30 | Steven |  | $3.88
171 | 2016-12-05 | New custom teams | Switch | Blue Toggle Switch 4pcs | AliExpress |  | 1 |  | 3.83 | AUD | 3.83 | https://www.aliexpress.com/item/DC12V-20A-Indicator-Panel-Mounting-ON-OFF-Car-Toggle-Switch-Red-green-yellow-blue/32397900424.html | CHOOSE BLUE | Approved |  | Arrived | 2016-12-07 | 23-45days | 2016-12-30 | Steven |  | $3.83
172 | 2016-12-05 | New custom teams | Switch | Green Toggle Switch 4pcs | AliExpress |  | 1 |  | 3.88 | AUD | 3.88 | https://www.aliexpress.com/item/DC12V-20A-Indicator-Panel-Mounting-ON-OFF-Car-Toggle-Switch-Red-green-yellow-blue/32397900424.html | CHOOSE GREEN | Approved | CHOOSE GREEN. Pack of 4. Order reduced from 2 to 1. | Arrived | 2016-12-06 | 23-45days | 2016-12-30 | Steven |  | $3.88
173 | 2016-12-05 | New custom teams | Capacitor | 1000uF, 16V | DigiKey | 399-6106-ND | 10 | 4 | 0.406 | AUD | 4.06 | http://www.digikey.com.au/product-detail/en/kemet/ESK108M016AH2AA/399-6106-ND/2712524 |  | Approved |  | Delivered | 2016-12-23 |  |  | Tristan |  | $4.06
174 | 2016-12-05 | New custom teams | Capacitor | 10uF, 16V | DigiKey | 445-8351-ND | 20 | 8 | 0.636 | AUD | 12.72 | http://www.digikey.com.au/product-detail/en/tdk-corporation/FK16X7R1E106K/445-8351-ND/2815281 |  | Approved |  | Delivered | 2016-12-23 |  |  | Tristan |  | $12.72
175 | 2016-12-05 | New custom teams | Spring Terminal | 2pin 50pcs | AliExpress |  | 1 | 0 | 13.76 | AUD | 13.76 | https://www.aliexpress.com/item/50pcs-lot-141R-2-54MM-free-screw-spring-formula-PCB-terminal-horizontal-2-3-4/32705600423.html | TELL SELLER YOU WANT 2-PIN, when ordering | Approved | TELL SELLER YOU WANT 2-PIN, when ordering | Delivered | 2016-12-06 | 20-41days | 2017-01-09 | Steven |  | $13.76
176 | 2016-12-05 | New custom teams | Battery Connector | XT-60 Male & Female | HobbyKing |  | 3 | 0 | 4.15 | AUD | 12.45 | http://www.hobbyking.com/hobbyking/store/uh_viewitem.asp?idproduct=43416 | Pack of 5 pairs | Approved |  | Arrived | 2017-02-05 | 3-10 days |  | Steven |  | $12.45
177 | 2016-12-05 | New custom teams | Plates | 2mm PVC | Mr Noy |  | 1 | 1 | 50 | AUD | 50.00 | [Plates] | Approximate price | Approved | Approximate cost | In progress |  |  |  | Mr Noy |  | $50.00
178 | 2016-12-05 | New custom teams | Cable holder | Adhesive 30pcs | Ebay |  | 1 |  | 1.64 | AUD | 1.64 | http://www.ebay.com.au/itm/30Pcs-Black-Adhesive-Car-Wire-Tie-Clips-Fixer-Drop-Clamp-Cord-Clip-Cable-Holder-/121542917457 |  | Combined with other order | See #91 |  |  |  |  | ----- |  | $0.00
179 | 2016-12-05 | New custom teams | Resistor | Kit 2600pcs 130 values | AliExpress |  | 1 |  | 14.17 | AUD | 14.17 | https://www.aliexpress.com/item/Hot-Sale-2600pcs-130-Values-1-4W-0-25W-1-Metal-Film-Resistors-Assorted-Pack-Kit/32662753709.html |  | Approved |  | Arrived | 2016-12-06 | 23-45days | 2017-01-07 | Steven |  | $14.17
180 | 2016-12-05 | New custom teams | Wire | Rainbow Ribbon Cable 40 way 1M | AliExpress |  | 2 |  | 2.86 | AUD | 5.66 | https://www.aliexpress.com/item/1M-3-3ft-40-Way-40-pin-Flat-Color-Rainbow-Ribbon-IDC-Cable-Wire-Rainbow-Cable/32703330248.html | Get 2 metres minimum | Approved | Get 2 metres minimum | Delivered | 2016-12-07 | 23-47days | 2016-12-30 | Steven |  | $5.66
181 | 2016-12-05 | New custom teams | Wire | 22AWG Black and Red 1M | AliExpress |  | 3 |  | 0.66 | AUD | 1.98 | https://www.aliexpress.com/item/Tinned-copper-22AWG-2-pin-Red-Black-cable-PVC-insulated-wire-22-awg-wire-Electric-cable/32597557917.html |  | Approved | 3 metres | Delivered | 2016-12-06 | 23-47days | 2016-12-30 | Steven |  | $1.98
182 | 2016-12-05 | New custom teams | Heat sink | TO-220 10pcs | eBay |  | 1 |  | 1.91 | AUD | 1.91 | http://www.ebay.com.au/itm/10pcs-Aluminum-Heatsink-Heat-Sink-with-Screw-Sets-TO-220-Transistor-20-15-10mm-/192026969497 |  | Approved |  | Delivered | 2016-12-06 | Thu. 22 Dec. and Tue. 17 Jan. | ~4/1/2016 | Steven |  | $1.91
208 | 2017-02-06 | New custom teams | Large tool box | With wheels | Bunnings |  | 1 | 0 | $99.00 | AUD | 99.00 | https://www.bunnings.com.au/stanley-mobile-tool-chest-with-organisers_p5563108 | Alternative similar item may be bought instead | Approved |  | Delivered | 2017-02-01 |  |  | Mr Noy | $0.00 | $99.00
210 | 2017-02-18 | New custom teams | Logic Level Converter | For MPU9250, pack of 5 | AliExpress |  | 1 | 0 | $1.72 | AUD | 1.72 | https://www.aliexpress.com/item/5PCS-Two-Channel-IIC-I2C-Logic-Level-Converter-Bi-Directional-Module-5V-to-3-3V/32278943189.html |  | Approved |  | Delivered | 2017-02-18 | 28-50 days | 2017-03-15 | Andrew |  | $1.72
212 | 2017 Feb | New custom teams | Wire | Black and Red, Retrospective | AliExpress |  | 5 | 0 | $0.64 | AUD | 3.20 |  |  | Approved |  | Delivered | 2017-02-01 |  | 2017-03-05 | Andrew |  | $3.20
246 | 2017-05-18 | New custom teams | Screw | 10mm Nylon CS | Ebay |  | 40 | 0 | 3.49 | AUD | 3.49 | http://www.ebay.com.au/itm/222159477082?var=521001560097 |  | Approved |  | Ordered | 2017-05-18 | 8/6/2017-30/7/2017 |  | Andrew |  | $3.49
247 | 2017-05-18 | New custom teams | Nut | Hex Nylon | Ebay |  | 100 |  | 1.19 | AUD | 1.19 | http://www.ebay.com.au/itm/Useful-Device-White-Nylon-Screw-Nuts-Hexagonal-Standoff-Spacer-M3-Nut-100-PcsIF2-/262924443320 |  | Approved |  | Ordered | 2017-05-18 | 6/6/2017-11/7/2017 |  | Andrew |  | $1.19
248 | 2017-05-19 | New custom teams | containers | They store stuff | Bunnings |  | 2 | 0 | $9.98 | AUD | $19.96 | https://www.bunnings.com.au/tactix-328-x-237-x-58mm-large-storage-container-with-divider_p2583556 |  | Denied | Will purchase individual boxes from Kmart instead |  |  |  |  | ----- |  | $0.00
249 | 2017-05-19 | New custom teams | containers | They store stuff | Kmart |  | 3 | 0 | $2 | AUD | $6.00 | http://www.kmart.com.au/product/small-plastic-food-storage-containers---250ml,-set-of-4/159805 |  | Approved |  | Delivered | 2017-05-24 |  | 2017-05-24 | Steven |  | $6.00
250 | 2017-05-19 | New custom teams | containers | They store stuff | Kmart |  | 3 | 0 | $2 | AUD | $6.00 | http://www.kmart.com.au/product/rectangle-plastic-food-storage-container---1.5l/159807 |  | Approved |  | Delivered | 2017-05-24 |  | 2017-05-24 | Steven |  | $6.00
253 | 2017-06-27 | New custom teams | Screws | M3x10mm, 100pcs | Ebay |  | 1 | 0 | 3.13 | AUD | 3.13 | http://www.ebay.com.au/itm/232264907512?var=531502738210 |  | Approved |  | Delivered | 2017-06-27 |  | 2017-07-14 | Andrew |  | $3.13
254 | 2017-06-27 | New custom teams | Standoffs | M3x30mm, 40pcs | Ebay |  | 1 | 0 | 6.97 | AUD | 6.97 | http://www.ebay.com.au/itm/322163383596?var=511073554388 |  | Approved |  | Arrived | 2017-06-27 |  | 2017-07-19 | Andrew |  | $6.97
255 | 2017-06-27 | New custom teams | Screws | M3x20mm, 100pcs | Ebay |  | 1 | 0 | 7.74 | AUD | 7.74 | http://www.ebay.com.au/itm/322161705655?var=511072516655 |  | Approved |  | Arrived | 2017-06-27 |  | 2017-07-19 | Andrew |  | $7.74
256 | 2017-06-27 | New custom teams | Standoffs | M3x25mm, M-F, 50pcs | Ebay |  | 1 | 0 | 6.55 | AUD | 6.55 | http://www.ebay.com.au/itm/322353117390?var=511271474848 |  | Approved |  | Delivered | 2017-06-27 |  | 2017-07-14 | Andrew |  | $6.55
257 | 2017-06-27 | New custom teams | Standoffs | M3x10mm, M-F, 50pcs | Ebay |  | 1 | 0 | 4.55 | AUD | 4.55 | http://www.ebay.com.au/itm/322353117390?var=511271474839 |  | Approved |  | Delivered | 2017-06-27 |  | 2017-07-14 | Andrew |  | $4.55
258 | 2017-06-27 | New custom teams | Screws | M3x10mm, nylon, 100pcs | Ebay |  | 1 | 0 | 1.6 | AUD | 1.60 | http://www.ebay.com.au/itm/172546230639 |  | Approved |  | Arrived | 2017-06-27 |  | 2017-07-19 | Andrew |  | $1.60
259 | 2017-06-27 | New custom teams | Resistor | 3.3k 100pcs | Ebay |  | 1 | 0 | 1.85 | AUD | 1.85 | http://www.ebay.com.au/itm/100Pcs-1-4W-Watt-3-3K-Ohm-3-3Kohm-0-25W-3300R-1-Metal-Film-Resistor-Ic-New-Q/302309392860 |  | Approved |  | Delivered | 2017-06-27 |  | 2017-08-03 | Andrew |  | $1.85
260 | 2017-06-27 | New custom teams | Resistor | 1k 100pcs | Ebay |  | 1 | 0 | 1 | AUD | 1.00 | http://www.ebay.com.au/itm/100-PCS-1-4W-0-25W-5-1-K-OHM-Carbon-Film-Resistor-1st-Class-Postage-UK-CT-/291965299214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 |  | Approved |  | Delivered | 2017-06-27 |  | 2017-07-14 | Andrew |  | $1.00
262 | 2017-06-27 | New custom teams | Wire | M-F 40pcs 20cm | Ebay |  | 1 | 1 | 1.39 | AUD | 2.78 | http://www.ebay.com.au/itm/40Pcs-Dupont-Wire-Jumper-Cables-10-20cm-M-M-M-F-F-F-1P-1P-For-Arduino-Breadboard-/192187563720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 |  | Approved |  | Delivered | 2017-06-27 |  | 2017-08-03 | Andrew |  | $2.78
263 | 2017-06-27 | New custom teams | XT60 Connector | 20pcs | Ebay |  | 1 | 0 | 6.38 | AUD | 6.38 | http://www.ebay.com.au/itm/2-20-40pcs-XT60-Male-Female-Bullet-Connectors-Plugs-for-RC-Lipo-Battery-New-/281903764882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 |  | Approved |  | Arrived | 2017-06-27 |  | 2017-07-19 | Andrew |  | $6.38
264 | 2017-06-27 | New custom teams | 5mm heatshrink | Black 1M | Ebay |  | 1 | 0 | 1.66 | AUD | 1.66 | http://www.ebay.com.au/itm/0-6mm-12mm-Black-2-1-Heat-Shrink-Tube-Tubing-Sleeving-Heatshrink-Wrap-Wire-Cable-/222207186237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 |  | Approved |  | Arrived | 2017-06-27 |  | 2017-07-18 | Andrew |  | $1.66
265 | 2017-06-27 | New custom teams | Logic Level Converter | 5pcs | Ebay |  | 1 | 0 | 2.39 | AUD | 2.39 | http://www.ebay.com.au/itm/1-2-5pcs-I2C-IIC-4-Channel-Logic-Level-Converter-Module-Bi-Directional-Arduino-/381322480561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 |  | Approved |  | Delivered | 2017-06-27 |  | 2017-08-03 | Andrew |  | $2.39
266 | 2017-06-27 | New custom teams | Screw | Steel, M3x10mm, 100pcs | Ebay |  | 1 | 0 | 2.22 | AUD | 2.22 | http://www.ebay.com.au/itm/100pcs-M3-304-Stainless-Steel-Cross-Flat-Countersunk-Head-Machine-Screws-Bolts-/232362952297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 |  | Approved | Shipped to Andrew and may arrive after he leaves | Delivered | 2017-06-27 |  | 2017-07-14 | Andrew |  | $2.22
267 | 2017-06-27 | New custom teams | Multimeter |  | Ebay |  | 1 | 0 | 23.72 | AUD | 23.72 | http://www.ebay.com.au/itm/Digitek-DT-4000P-2-Pocket-Digital-Multimeter-4000-count-Autorange-0-5-Accuracy-/171046640758 |  | Approved | Shipped to Andrew and may arrive after he leaves | Ordered | 2017-06-27 |  |  | Andrew |  | $23.72
268 | 2017-06-27 | New custom teams | LR44 1.5V battery | 10pcs for multimeter | Ebay |  | 1 | 0 | 1.1.3 | AUD | 1.13 | http://www.ebay.com.au/itm/10pcs-AG13-LR44-L1154-357-303-1-5V-Alkaline-Button-Cell-Battery-for-watch-camera-/292071282143 |  | Approved |  | Delivered | 2017-06-27 |  | 2017-08-03 | Andrew |  | $1.13
273 | 2017-06-27 | New custom teams | Standoff kit | 90 Pcs 10mm standoff kit, 30 M3 10mm Spacers, 60 M3 6mm nylon | Ebay |  | 1 | 0 | 12.2 | AUD | 12.20 | http://www.ebay.com.au/itm/90-Pcs-10mm-standoff-kit-30-M3-10mm-Spacers-60-M3-6mm-nylon-plastic-screws-PCB-/331918023712 |  | Approved | Added retrospectively | Delivered | 2017-06-28 |  |  | Andrew |  | $12.20
274 | 2017-06-29 | New custom teams | Screws | 100pcs, M3x10mm | Ebay |  | 1 | 0 | 1.6 | AUD | 1.60 | http://www.ebay.com.au/itm/100-Pcs-M3x10mm-Threaded-Rod-White-Nylon-Phillips-Head-Screws-Bolts-WS-/222458743674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 |  | Approved |  | Ordered | 2017-06-29 | 18/7 to 22/8 |  | Andrew |  | $1.60
275 | 2017-07-12 | New custom teams | Standoff | Standoff M3 35mm M-F Nylon | Aliexpress |  | 25 | 3 |  | USD | $3.82 | https://www.aliexpress.com/item/M3-35-6-1-pcs-Black-Nylon-Standoff-Spacer-Standard-M3-Male-Female-35mm-Standoff-Kit/32679681298.html |  | Denied | Replaced with #280 for faster delivery. Supplemented by orders #256, 257 |  |  |  |  | Steven | $0.96 | $0.00
276 | 2017-07-12 | New custom teams | Screw | Screw M3 20mm Round Steel | Aliexpress |  | 1 | 10 |  | USD | $2.52 | https://www.aliexpress.com/item/304-stainless-steel-Phillips-head-Machine-Screw-Phillips-pan-head-screws-M3-20mm/32354857582.html |  | Approved | Supplemented by #281 | Ordered | 2017-07-18 | 23-47days |  | Steven |  | $2.52
277 | 2017-07-12 | New custom teams | Nut | Nut M3 N/A Hex Steel | Ebay |  | 50 | 4 | $2.43 | AUD | $2.43 | http://www.ebay.com.au/itm/M3-M4-M5-M6-M8-M10-M12-M14-M18-M20-M24-DIN934-316-A4-Stainless-Steel-Hex-Nuts-/222284402394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 |  | Approved | Supplemented by #282 | Delivered | 2017-07-18 | Fri. 4 Aug. and Mon. 11 Sep. |  | Steven |  | $2.43
278 | 2017-07-12 | New custom teams | Screw | Screw M3 10mm Countersunk Steel | Aliexpress |  | 32 |  |  | USD | $5.48 | https://www.aliexpress.com/item/M3-X-10Mm-Metric-304-Stainless-Steel-Hex-Socket-Countersunk-Flat-Head-Screw-Bolts-100Pcs/32765963749.html |  | Denied | No longer available. I will also not order hex bolts due to wear |  |  |  |  | Steven |  | $0.00
279 | 2017-07-12 | New custom teams | Screw | Screw M3 6mm Countersunk Nylon | Ebay |  | 20 | 4 |  |  | $2.48 | http://www.ebay.com.au/itm/M3-3mm-Nylon-Flat-Head-Phillips-Screws-Countersunk-head-Machine-Screws-Black-/322159904729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 |  | Approved | Pack of 30 purchased | Delivered | 2017-07-18 | between Fri. 4 Aug. and Mon. 11 Sep. |  | Steven |  | $2.48
280 | 2017-07-12 | New custom teams | Standoff | M3 x 35mm+5mm Nylon Hexagonal Screw Nut Male Female Standoff Spacer 20 Pcs | Ebay |  | 1 | 0 | 5.74 | AUD | 5.74 | http://www.ebay.com.au/itm/M3-x-35mm-5mm-Nylon-Hexagonal-Screw-Nut-Male-Female-Standoff-Spacer-20-Pcs-/301719328693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 |  | Approved | Replaces #275. Supplemented by orders #256, 257 | Delivered | 2017-07-18 | Fri. 4 Aug. and Fri. 18 Aug |  | Steven |  | $5.74
281 | 2017-07-12 | New custom teams | Screw | Qty 20 Pan Head M3 (3mm) x 20mm Stainless Steel Machine Screw 304 Phillip Bolt Qty 20 Pan Head M3 (3mm) x 20mm Stainless Steel Machine Screw 304 Phillip Bolt Qty 20 Pan Head M3 (3mm) x 20mm Stainless Steel Machine Screw 304 Phillip Bolt Qty 20 Pan Head M3 (3mm) x 20mm Stainless Steel Machine Screw 304 Phillip Bolt | Ebay |  | 1 | 0 | 5.3 | AUD | 5.30 | http://www.ebay.com.au/itm/181842374471 |  | Approved | Supplements #276. Arrives quicker | Delivered | 2017-07-18 | Mon. 24 Jul. | 2017-08-03 | Steven |  | $5.30
282 | 2017-07-12 | New custom teams | Nut | 20 pcs M3 3mm Stainless Steel Hex Nut | Ebay |  | 20 |  | $3.95 | AUD | $3.95 | http://www.ebay.com.au/itm/M3-M4-M5-M6-M8-M10-M12-M14-M18-M20-M24-DIN934-316-A4-Stainless-Steel-Hex-Nuts-/222284402394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 |  | Approved | Supplements #277. Arrives quicker | Delivered | 2017-07-18 | Fri. 21 Jul. and Tue. 25 Jul. | 2017-08-03 | Steven |  | $3.95
283 | 2017-07-12 | New custom teams | Screw | M3 304 Stainless Steel Phillips Cross Recessed Flat Countersunk Head Screws Bolt | Ebay |  | 100 |  | $5.29 | AUD | $5.29 | http://www.ebay.com.au/itm/M3-304-Stainless-Steel-Phillips-Cross-Recessed-Flat-Countersunk-Head-Screws-Bolt-/322291209661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 |  | Approved | Replaces #278. Cheaper, quicker, better | Delivered | 2017-07-18 | Thu. 3 Aug. and Thu. 17 Aug | 2017-08-03 | Steven |  | $5.29
286 | 2017-08-05 | New custom teams | L298 Motor Controller |  | eBay |  | 2 | 1 | $5.39 | AUD | $10.78 | http://www.ebay.com.au/itm/371541113308 |  | Approved | Supplier changed from https://www.aliexpress.com/item/New-Dual-H-Bridge-DC-Stepper-Motor-Drive-Controller-Board-Module-L298N-for-arduino/32581976321.html | Ordered | 2017-08-06 | Thu. 10 Aug. and Wed. 16 Aug. |  | Steven |  | $10.78
287 | 2017-08-05 | New custom teams | MPU 9250 | Accelerometer, Gyroscope, Magnetometer, 3 Axis Sensor I²C, SPI Output | eBay |  | 2 | 1 | $7.75 | AUD | $15.50 | http://www.ebay.com.au/itm/162276581190 |  | Approved | Supplier changed from https://www.digikey.com.au/product-detail/en/tdk-invensense/MPU-9250/1428-1019-2-ND/4626449 | Ordered | 2017-08-06 | Thu. 10 Aug. and Wed. 16 Aug. |  | Steven |  | $15.50
288 | 2017-08-05 | New custom teams | Arduino MEGA 2560 | Microcontroller | Ebay |  | 2 | 2 | $16.95 | AUD | $33.90 | http://www.ebay.com.au/itm/Arduino-Mega-R3-with-USB-Cable-FREE-SHIPPING-FROM-BRISBANE-AU-/132265448660 |  | Approved | Order increased from 1 to 2 units. Changed link from http://www.ebay.com.au/itm/Mega-2560-R3-REV3-ATmega2560-16AU-Board-USB-Cable-Compatible-For-Arduino-LKAN-/351895746273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 | Delivered | 2017-08-06 | Thu. 10 Aug. |  | Steven |  | $33.90
289 | 2017-08-05 | New custom teams | Standoffs | 25mm M3 Nylon | Ebay |  | 1 | 1 | $6.11 | AUD | $6.11 | http://www.ebay.com.au/itm/30-Pcs-M3-25mm-6mm-Female-Male-White-Nylon-Hex-PCB-Stand-Off-Screw-Spacer-/331640608206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 | Could potentially be sold out. | Denied | Use existing stock. A bunch of standoffs were delivered last week. If they are too long, you can cut them. |  |  |  |  | ----- |  | $0.00
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

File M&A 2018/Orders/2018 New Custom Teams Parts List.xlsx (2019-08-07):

New Custom Teams Parts List
Total for 2 teams - Bogahawatta, Feros; and Cranitch, Gannon, Hunter
Team | Item | Description | Supplier | Vendor PN | Total QTY (inc. spares) | Spares | Price per unit in original currency | Original Currency | Total price (AUD) | Link | Notes
Manufactured Parts
New custom teams | Plates
New custom teams | TSOP ring
New custom teams | 3D printed parts | Excluding TSOP ring
Motor Assembly
New custom teams | Motor | 25mm diameter 500rpm | AliExpress |  | 20 | 3 | 11.43 | AUD | 206.10 | https://www.aliexpress.com/item/DC-12V-500RPM-25GA-40mA-High-Torque-Electric-Gear-Box-Motor-25MM/32270478250.html | Including shipping
New custom teams | Motor controller | L298n dual | AliExpress |  | 16 | 4 | 2.01 | AUD | 45.13 | https://www.aliexpress.com/item/Free-shipping-1pcs-lot-Special-promotions-2pcs-lot-L298N-motor-driver-board-module-stepper-motor-smart/1872427142.html | Including shipping
New custom teams | Wheels | Kornylak omni-wheels | BBC |  | 0 | 0 | NA | NA | 0.00 |  | Already in stock
New custom teams | Wheel Hubs | Pololu Universal Aluminum Mounting Hub for 4mm Shaft, #4-40 Holes | Pololu |  | 3 | 3 | 6.12 | USD | 23.25 | https://www.pololu.com/product/1997 | Pack of 2
New custom teams | Motor mount |  | AliExpress |  | 24 | 4 | 1.2 | AUD | 30.82 | https://www.aliexpress.com/item/Aluminium-alloy-25mm-25GB-GA-gear-motor-Bracket-with-Matching-screw/32660288599.html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 | Including shipping
Parkour Legend
New custom teams | Microcontroller | Arduino Mega 2560 | Ebay
Power circuit
New custom teams
New custom teams
New custom teams
Light sensors
New custom teams | LDR | 50pcs | Ebay |  | 1 |  |  |  | 2.43 | http://www.ebay.com.au/itm/50pcs-Photo-Light-Sensitive-Resistor-GL5528-Photoresistor-Photocell-LDR-5mm-/291568788812
New custom teams | LED | 5mm Red 100pcs | Ebay |  | 1 |  | 1.05 | AUD | 1.05 | http://www.ebay.com.au/itm/281632283748
New custom teams
New custom teams
New custom teams
New custom teams
Other sensors
New custom teams | TSOPs
New custom teams | IMU | MPU9250 | AliExpress |  | 10 | 4 | 4.62 | AUD | 46.20 | https://www.aliexpress.com/item/MPU-9250-GY-9250-9-axis-sensor-module-I2C-SPI-Communications-Thriaxis-gyroscope-accelerometer-triaxial-magnetic/1904077579.html | This is basically your compass sensor
New custom teams
New custom teams
New custom teams
New custom teams
Fasteners
New custom teams | Screws | M3x10mm, 100pcs | Ebay |  | 1 | 0 | 3.13 | AUD | 3.13 | http://www.ebay.com.au/itm/232264907512?var=531502738210
New custom teams | Standoffs | M3x30mm, 40pcs | Ebay |  | 1 | 0 | 6.97 | AUD | 6.97 | http://www.ebay.com.au/itm/322163383596?var=511073554388
New custom teams | Screws | M3x20mm, 100pcs | Ebay |  | 1 | 0 | 7.74 | AUD | 7.74 | http://www.ebay.com.au/itm/322161705655?var=511072516655
New custom teams | Standoffs | M3x25mm, M-F, 50pcs | Ebay |  | 1 | 0 | 6.55 | AUD | 6.55 | http://www.ebay.com.au/itm/322353117390?var=511271474848
New custom teams | Standoffs | M3x10mm, M-F, 50pcs | Ebay |  | 1 | 0 | 4.55 | AUD | 4.55 | http://www.ebay.com.au/itm/322353117390?var=511271474839
New custom teams | Screws | M3x10mm, nylon, 100pcs | Ebay |  | 1 | 0 | 1.6 | AUD | 1.60 | http://www.ebay.com.au/itm/172546230639
New custom teams | Screw | 10mm Nylon CS | Ebay |  | 40 | 0 | 3.49 | AUD | 3.49 | http://www.ebay.com.au/itm/222159477082?var=521001560097
New custom teams | Nut | Hex Nylon | Ebay |  | 100 |  | 1.19 | AUD | 1.19 | http://www.ebay.com.au/itm/Useful-Device-White-Nylon-Screw-Nuts-Hexagonal-Standoff-Spacer-M3-Nut-100-PcsIF2-/262924443320
New custom teams | Screw | Steel, M3x10mm, 100pcs | Ebay |  | 1 | 0 | 2.22 | AUD | 2.22 | http://www.ebay.com.au/itm/100pcs-M3-304-Stainless-Steel-Cross-Flat-Countersunk-Head-Machine-Screws-Bolts-/232362952297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
New custom teams | Standoff kit | 90 Pcs 10mm standoff kit, 30 M3 10mm Spacers, 60 M3 6mm nylon | Ebay |  | 1 | 0 | 12.2 | AUD | 12.20 | http://www.ebay.com.au/itm/90-Pcs-10mm-standoff-kit-30-M3-10mm-Spacers-60-M3-6mm-nylon-plastic-screws-PCB-/331918023712
New custom teams | Screws | 100pcs, M3x10mm | Ebay |  | 1 | 0 | 1.6 | AUD | 1.60 | http://www.ebay.com.au/itm/100-Pcs-M3x10mm-Threaded-Rod-White-Nylon-Phillips-Head-Screws-Bolts-WS-/222458743674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
New custom teams | Standoff | Standoff M3 35mm M-F Nylon | Aliexpress |  | 25 | 3 |  | USD | $3.82 | https://www.aliexpress.com/item/M3-35-6-1-pcs-Black-Nylon-Standoff-Spacer-Standard-M3-Male-Female-35mm-Standoff-Kit/32679681298.html
New custom teams | Screw | Screw M3 20mm Round Steel | Aliexpress |  | 1 | 10 |  | USD | $2.52 | https://www.aliexpress.com/item/304-stainless-steel-Phillips-head-Machine-Screw-Phillips-pan-head-screws-M3-20mm/32354857582.html
New custom teams | Nut | Nut M3 N/A Hex Steel | Ebay |  | 50 | 4 | $2.43 | AUD | $2.43 | http://www.ebay.com.au/itm/M3-M4-M5-M6-M8-M10-M12-M14-M18-M20-M24-DIN934-316-A4-Stainless-Steel-Hex-Nuts-/222284402394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
New custom teams | Screw | Screw M3 10mm Countersunk Steel | Aliexpress |  | 32 |  |  | USD | $5.48 | https://www.aliexpress.com/item/M3-X-10Mm-Metric-304-Stainless-Steel-Hex-Socket-Countersunk-Flat-Head-Screw-Bolts-100Pcs/32765963749.html
New custom teams | Screw | Screw M3 6mm Countersunk Nylon | Ebay |  | 20 | 4 |  |  | $2.48 | http://www.ebay.com.au/itm/M3-3mm-Nylon-Flat-Head-Phillips-Screws-Countersunk-head-Machine-Screws-Black-/322159904729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
New custom teams | Standoff | M3 x 35mm+5mm Nylon Hexagonal Screw Nut Male Female Standoff Spacer 20 Pcs | Ebay |  | 1 | 0 | 5.74 | AUD | 5.74 | http://www.ebay.com.au/itm/M3-x-35mm-5mm-Nylon-Hexagonal-Screw-Nut-Male-Female-Standoff-Spacer-20-Pcs-/301719328693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
New custom teams | Screw | Qty 20 Pan Head M3 (3mm) x 20mm Stainless Steel Machine Screw 304 Phillip Bolt Qty 20 Pan Head M3 (3mm) x 20mm Stainless Steel Machine Screw 304 Phillip Bolt Qty 20 Pan Head M3 (3mm) x 20mm Stainless Steel Machine Screw 304 Phillip Bolt Qty 20 Pan Head M3 (3mm) x 20mm Stainless Steel Machine Screw 304 Phillip Bolt | Ebay |  | 1 | 0 | 5.3 | AUD | 5.30 | http://www.ebay.com.au/itm/181842374471
New custom teams | Nut | 20 pcs M3 3mm Stainless Steel Hex Nut | Ebay |  | 20 |  | $3.95 | AUD | $3.95 | http://www.ebay.com.au/itm/M3-M4-M5-M6-M8-M10-M12-M14-M18-M20-M24-DIN934-316-A4-Stainless-Steel-Hex-Nuts-/222284402394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
New custom teams | Screw | M3 304 Stainless Steel Phillips Cross Recessed Flat Countersunk Head Screws Bolt | Ebay |  | 100 |  | $5.29 | AUD | $5.29 | http://www.ebay.com.au/itm/M3-304-Stainless-Steel-Phillips-Cross-Recessed-Flat-Countersunk-Head-Screws-Bolt-/322291209661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
New custom teams | Standoffs | 25mm M3 Nylon | Ebay |  | 1 | 1 | $6.11 | AUD | $6.11 | http://www.ebay.com.au/itm/30-Pcs-M3-25mm-6mm-Female-Male-White-Nylon-Hex-PCB-Stand-Off-Screw-Spacer-/331640608206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 | Could potentially be sold out.
Battery
New custom teams | Battery Charger | Turnigy TQ4 4x6s | HobbyKing |  | 1 | 0 | 96.47 | AUD | 96.47 | https://hobbyking.com/en_us/turnigy-4x6s-lithium-polymer-battery-pack-charger.html
New custom teams | Power Supply | Turnigy Reaktor Pro 350W 23A Power Supply (100~240V AC) | HobbyKing |  | 1 | 0 | 72.33 | AUD | 72.33 | https://hobbyking.com/en_us/turnigy-reaktor-pro-350w-23a-power-supply-100-240v-ac.html
New custom teams | Power Cable | IEC C5 1.8m | Jaycar |  | 2 |  | 6.95 | AUD | 13.90 | https://www.jaycar.com.au/3pin-mains-plug-to-iec-c5-clover-leaf-1-8m/p/PS4120
New custom teams | Lipo Bags |  |  |  | 0 |  |  |  | 0.00
New custom teams | Battery Connector | XT-60 Male & Female | HobbyKing |  | 3 | 0 | 4.15 | AUD | 12.45 | http://www.hobbyking.com/hobbyking/store/uh_viewitem.asp?idproduct=43416 | Pack of 5 pairs
New custom teams | XT60 Connector | 20pcs | Ebay |  | 1 | 0 | 6.38 | AUD | 6.38 | http://www.ebay.com.au/itm/2-20-40pcs-XT60-Male-Female-Bullet-Connectors-Plugs-for-RC-Lipo-Battery-New-/281903764882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
New custom teams | Battery | Turnigy 1000mAh 3S | HobbyKing |  | 12 | 0 | 15.34 | AUD | 184.08 | https://hobbyking.com/en_us/turnigy-nano-tech-1000mah-3s-25-50c-lipo-pack.html
Shared | Power Cable for Battery Charger | Cosmol Male 3 Pin Plug to Female IEC-C5 Plug 2m | Officeworks | COPCC502 | 5 | 0 | 14.88 | AUD | 74.4 | http://www.officeworks.com.au/shop/officeworks/p/comsol-male-3-pin-plug-to-female-iec-c5-plug-2m-copcc502
Shared | JST-XH Balance Board | For Charger | Ebay |  | 3 | 0 | $1.73 | AUD | 5.19 | http://www.ebay.com.au/itm/JST-XH-2S-6S-Balance-Charger-Expansion-Adapter-Board-RC-Lipo-Battery-Charging-/262688838187
Shared | XT60 to 4mm banana | For Charger | Ebay |  | 4 | 0 | $2.39 | AUD | 9.56 | http://www.ebay.com.au/itm/XT60-Charger-Cable-Connector-to-4mm-Banana-Bullet-Wire-Plug-Battery-Connectors-/291985407760
Wiring
New custom teams | Veroboard | 40pc pack | Banggood |  | 2 | 0 | 14.07 | AUD | 28.14 | http://www.banggood.com/40Pcs-FR-4-Double-Side-Prototype-PCB-Printed-Circuit-Board-p-995732.html
New custom teams | Stripboard | 40pc pack | Banggood |  | 3 | 0 | 14.43 | AUD | 43.29 | http://www.banggood.com/40Pcs-FR-4-Double-Side-Prototype-PCB-Printed-Circuit-Board-p-995732.html | Pack of 3
New custom teams | Jumper Wires | 20cm, F-F, M-F, M-M | AliExpress |  | 2 |  | 4.12 | AUD | 8.24 | https://www.aliexpress.com/item/free-shipping-Dupont-line-120pcs-20cm-male-to-male-male-to-female-and-female-to-female/32668758951.html
New custom teams | Jumper Wires | 10cm, F-F, M-F, M-M | AliExpress |  | 2 |  | 2.66 | AUD | 5.32 | https://www.aliexpress.com/item/Dupont-line-120pcs-10cm-male-to-male-male-to-female-and-female-to-female-jumper/32328010671.html
Shared | Female Headers | 50pcs | Ebay |  | 1 | 0 | 7.44 | AUD | 7.44 | http://www.ebay.com.au/itm/50Pcs-2-54Mm-40-Pin-Female-Strip-Single-Row-Pin-Header-New-Diy-Ic-Develope-P-/282282594772
New custom teams | Switch | Red Toggle Switch 4pcs | AliExpress |  | 1 |  | 3.88 | AUD | 3.88 | https://www.aliexpress.com/item/DC12V-20A-Indicator-Panel-Mounting-ON-OFF-Car-Toggle-Switch-Red-green-yellow-blue/32397900424.html | CHOOSE RED
New custom teams | Switch | Blue Toggle Switch 4pcs | AliExpress |  | 1 |  | 3.83 | AUD | 3.83 | https://www.aliexpress.com/item/DC12V-20A-Indicator-Panel-Mounting-ON-OFF-Car-Toggle-Switch-Red-green-yellow-blue/32397900424.html | CHOOSE BLUE
New custom teams | Switch | Green Toggle Switch 4pcs | AliExpress |  | 1 |  | 3.88 | AUD | 3.88 | https://www.aliexpress.com/item/DC12V-20A-Indicator-Panel-Mounting-ON-OFF-Car-Toggle-Switch-Red-green-yellow-blue/32397900424.html | CHOOSE GREEN
New custom teams | Fuse | 2A 20pcs | AliExpress |  | 2 |  | 1.37 | AUD | 2.74 | https://www.aliexpress.com/item/20Pcs-Lot-2A-ATM-Mini-Blade-Fuse-Assortment-Auto-Car-Motorcycle-SUV-FUSES/32683738472.html | TELL SELLER YOU WANT 2A
New custom teams | Fuse | 7.5A 50pcs | AliExpress |  | 1 |  | 3 | AUD | 3.00 | https://www.aliexpress.com/item/High-Quality-50pcs-New-Car-Auto-Truck-Mini-Blade-Small-7-5A-Fuses-VE402-P/32751599689.html
New custom teams | Fuse Holder | MINI Fuse Holder, vertical, 50 pack | AliExpress |  | 1 |  | 26.72 | AUD | 26.60 | https://www.aliexpress.com/item/SL-1538-MINI-Style-Blade-Fuse-Holers-PCB-Mount-Fuse-holders-0153008/503553051.html
New custom teams | Spring Terminal | 2pin 50pcs | AliExpress |  | 1 | 0 | 13.76 | AUD | 13.76 | https://www.aliexpress.com/item/50pcs-lot-141R-2-54MM-free-screw-spring-formula-PCB-terminal-horizontal-2-3-4/32705600423.html | TELL SELLER YOU WANT 2-PIN, when ordering
New custom teams | Heat shrink | Assorted, black | eBay |  | 1 | 0 | 2.97 | AUD | 2.97 | http://www.ebay.com.au/itm/127-PCS-Heat-Shrink-Sleeve-Tube-Electrical-Cable-Tubing-Wrap-Wire-Kit-Assortment-/262445941840
New custom teams | Solid core wire | 6x25ft - 45.72m | Adafruit |  | 1 | 0 | 15.95 | USD | 19.19 | https://www.adafruit.com/product/1311
New custom teams | Wire | M-F 40pcs 20cm | Ebay |  | 1 | 1 | 1.39 | AUD | 2.78 | http://www.ebay.com.au/itm/40Pcs-Dupont-Wire-Jumper-Cables-10-20cm-M-M-M-F-F-F-1P-1P-For-Arduino-Breadboard-/192187563720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
New custom teams | Wire | Solid Core - Black | DigiKey |  | 2 | 0 | 3.28 | AUD | 6.56 | https://www.digikey.com.au/scripts/DkSearch/dksus.dll?Detail&itemSeq=236868673&uq=636394236786120994 | Added to reach free shipping
New custom teams | Wire | Solid Core - Red | DigiKey |  | 2 | 0 | 3.28 | AUD | 6.56 | https://www.digikey.com.au/scripts/DkSearch/dksus.dll?Detail&itemSeq=236868675&uq=636394236786120994 | Added to reach free shipping
New custom teams | Wire | Stranded - Black | DigiKey |  | 1 | 0 | 3.87 | AUD | 3.87 | https://www.digikey.com.au/scripts/DkSearch/dksus.dll?Detail&itemSeq=236868757&uq=636394236786120994 | Added to reach free shipping
New custom teams | Wire | Stranded - Red | DigiKey |  | 1 | 0 | 3.28 | AUD | 3.87 | https://www.digikey.com.au/scripts/DkSearch/dksus.dll?Detail&itemSeq=236868758&uq=636394236786120994 | Added to reach free shipping
New custom teams | Solid core wire | Black, 25ft | Adafruit |  | 1 | 0 | 2.95 | AUD | 3.55 | http://www.ebay.com.au/itm/322206432543?var=511111368469
New custom teams | Solid core wire | Red, 25ft | Adafruit |  | 1 | 0 | 2.95 | AUD | 3.55 | http://www.ebay.com.au/itm/322206432543?var=511111368469
New custom teams | Heat shrink | 1.5mm, 5m length, transparent | eBay |  | 1 | 0 | 2.08 | AUD | 2.08 | http://www.ebay.com.au/itm/322206432543?var=511111368469 | Replacement for #204
New custom teams | Heat shrink | 1mm, 2m | eBay |  | 1 | 0 | 4.5 | AUD | 4.50 | http://www.ebay.com.au/itm/Heat-Shrink-Black-2M-Tubing-11-Sizes-Cable-Insulation-Wire-Sleeve-Ratio-2-1-/272210814482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 | Urgent replacement for #204 until #241 arrives. Aus supplier
New custom teams | Heat shrink | 1.5mm, 5m length, transparent | eBay |  | 1 | 0 | 2.08 | AUD | 2.08 | http://www.ebay.com.au/itm/322206432543?var=511111368469
New custom teams | Wire | Rainbow Ribbon Cable 40 way 1M | AliExpress |  | 2 |  | 2.86 | AUD | 5.66 | https://www.aliexpress.com/item/1M-3-3ft-40-Way-40-pin-Flat-Color-Rainbow-Ribbon-IDC-Cable-Wire-Rainbow-Cable/32703330248.html | Get 2 metres minimum
New custom teams | Wire | 22AWG Black and Red 1M | AliExpress |  | 3 |  | 0.66 | AUD | 1.98 | https://www.aliexpress.com/item/Tinned-copper-22AWG-2-pin-Red-Black-cable-PVC-insulated-wire-22-awg-wire-Electric-cable/32597557917.html
New custom teams | Adhesive heat shrink | 1.6mm, 2m length, transparent | eBay |  | 1 | 0 |  |  | 3.55 | http://www.ebay.com.au/itm/1-6mm-25-4mm-Adhesive-Lined-3-1-Double-Wall-Heat-Shrink-Tube-Tubing-Waterproof-/262607660093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
New custom teams | Heat shrink | Assorted, black | eBay |  | 1 | 0 | 2.97 | AUD | 2.97 | http://www.ebay.com.au/itm/127-PCS-Heat-Shrink-Sleeve-Tube-Electrical-Cable-Tubing-Wrap-Wire-Kit-Assortment-/262445941840
New custom teams | Wire | Black and Red, Retrospective | AliExpress |  | 5 | 0 | $0.64 | AUD | 3.20
New custom teams | Cable holder | Adhesive 30pcs | Ebay |  | 1 |  | 1.64 | AUD | 1.64 | http://www.ebay.com.au/itm/30Pcs-Black-Adhesive-Car-Wire-Tie-Clips-Fixer-Drop-Clamp-Cord-Clip-Cable-Holder-/121542917457
Tools
New custom teams | containers | They store stuff | Bunnings |  | 2 | 0 | $9.98 | AUD | $19.96 | https://www.bunnings.com.au/tactix-328-x-237-x-58mm-large-storage-container-with-divider_p2583556
New custom teams | containers | They store stuff | Kmart |  | 3 | 0 | $2 | AUD | $6.00 | http://www.kmart.com.au/product/small-plastic-food-storage-containers---250ml,-set-of-4/159805
New custom teams | containers | They store stuff | Kmart |  | 3 | 0 | $2 | AUD | $6.00 | http://www.kmart.com.au/product/rectangle-plastic-food-storage-container---1.5l/159807
New custom teams | Large tool box | With wheels | Bunnings |  | 1 | 0 | $99.00 | AUD | 99.00 | https://www.bunnings.com.au/stanley-mobile-tool-chest-with-organisers_p5563108 | Alternative similar item may be bought instead
Shared | Tweezers | Precision Tweezers | Aliexpress |  | 2 | 7.8 |  | AUD | 15.60 | https://www.aliexpress.com/item/blackhead-tweezer-acne-clip-Professional-tweezer-stainless-steel-anti-magnetic-anti-static-tweezers-clip-acne-beauty/327042580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 | One of each
Shared | Wire Snips |  | Aliexpress |  | 4 |  | 1.71 | USD | 11.24 | https://www.aliexpress.com/item/P00337-Electrical-Wire-Cable-Cutters-Cutting-Side-Snips-Flush-Pliers-Nipper-Hand-Tools-Herramientas/32686834481.html | Including shipping
Shared | Solder Sucker | Metal Desoldering Pump Sucker Solder Irons Remvoal Remover Tool Blue Silver | eBay |  | 3 | 0 | 2.42 | USD | 9.75 | http://www.ebay.com/itm/Metal-Desoldering-Pump-Sucker-Solder-Irons-Removal-Remover-Tool-Blue-Silver-/351065197104
New custom teams | Allen Key Inches | 10Pcs Hexagon Key Allen Wrench Set 1/16 5/64 3/32 1/8 5/32 3/16 7/32 1/4 3/8 | eBay |  | 1 | 0 | 1.68 | USD | 2.13 | http://www.ebay.com/itm/10Pcs-Hexagon-Key-Allen-Wrench-Set-1-16-5-64-3-32-1-8-5-32-3-16-7-32-1-4-3-8-/263133244906
New custom teams | Allen Key mm | 10 x Metric/Imperial Wrench Set Allen Hex Hexagon Key With Keyring | eBay |  | 1 | 0 | 1.69 | USD | 2.14 | http://www.ebay.com/itm/10-x-Metric-Imperial-Wrench-Set-Allen-Hex-Hexagon-Key-With-Keyring-/222408074887
New custom teams | Allen Key Inches | 10Pcs Hexagon Key Allen Wrench Set 1/16 5/64 3/32 1/8 5/32 3/16 7/32 1/4 3/8 | eBay |  | 1 | 0 | 5.09 | AUD | 5.09 | http://www.ebay.com.au/itm/10Pcs-Hexagon-Key-Allen-Wrench-Set-1-16-5-64-3-32-1-8-5-32-3-16-7-32-1-4-3-8-AU-/162119550395
New custom teams | Allen Key mm | 10 x Metric/Imperial Wrench Set Allen Hex Hexagon Key With Keyring | eBay |  | 1 | 0 | 2.49 | AUD | 2.49 | http://www.ebay.com.au/itm/10PC-Metric-Hex-Hexagon-Allen-Alan-Key-Wrench-Set-1-5mm-10mm-With-Keyring-/322450773045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
Work-in-progress section
New custom teams | Diode | 10A 45V Shottky | DigiKey | SR1045-TPMSCT-ND | 10 | 4 | 0.91 | AUD | 9.10 | http://www.digikey.com.au/product-detail/en/micro-commercial-co/SR1045-TP/SR1045-TPMSCT-ND/2334476
New custom teams | Voltage Regulator | LM7805 2A 5V | DigiKey | 497-1468-5-ND | 10 | 4 | 0.819 | AUD | 8.19 | http://www.digikey.com.au/product-detail/en/stmicroelectronics/L78S05CV/497-1468-5-ND/585989
New custom teams | Capacitor | 1000uF, 16V | DigiKey | 399-6106-ND | 10 | 4 | 0.406 | AUD | 4.06 | http://www.digikey.com.au/product-detail/en/kemet/ESK108M016AH2AA/399-6106-ND/2712524
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

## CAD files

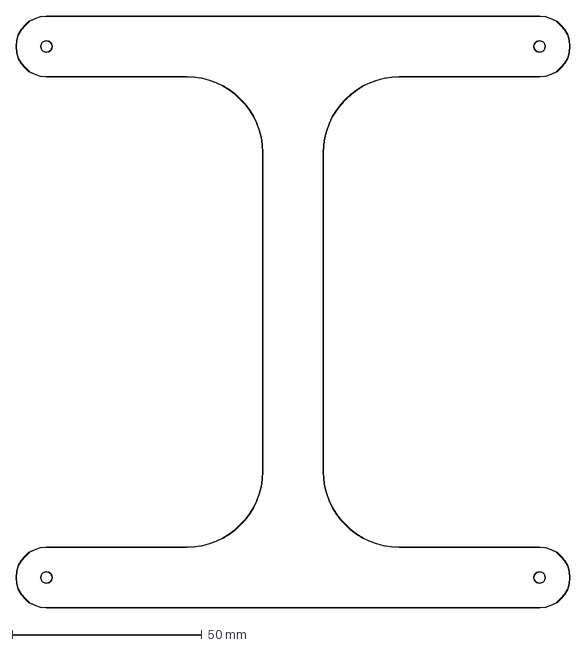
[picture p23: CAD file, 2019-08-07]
M&A 2018/Hardware/Maxon Parts/HandleMain.dxf
146.0 x 156.0 mm

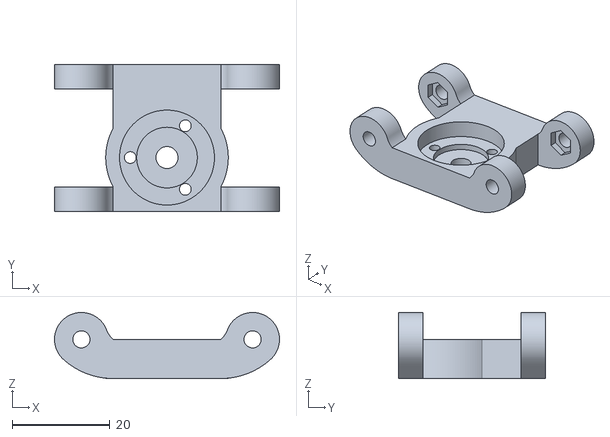
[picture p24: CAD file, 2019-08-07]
M&A 2019/Hardware/Design/Motor Main.stl
46.0 x 30.0 x 13.5

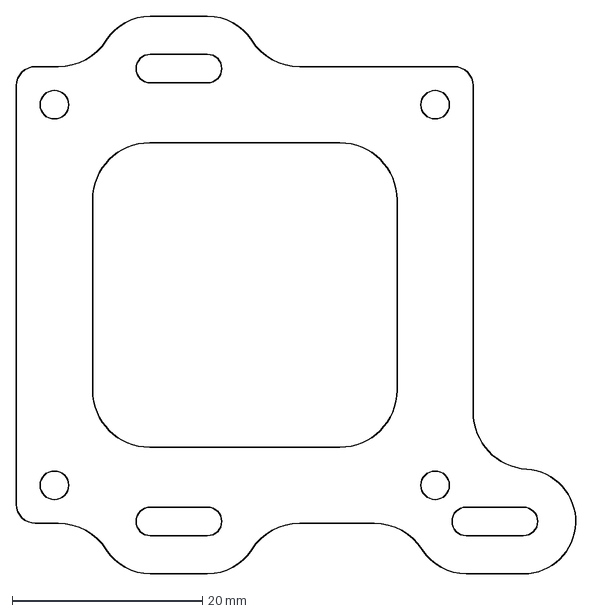
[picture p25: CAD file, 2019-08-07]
M&A 2018/Hardware/Maxon Parts/Laser Cut/Pixy Mount - 3.dxf
58.9 x 58.6 mm

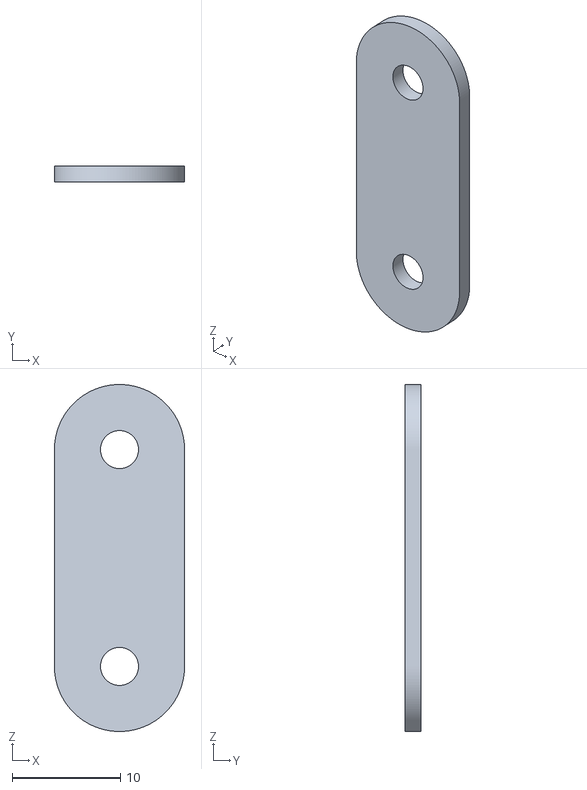
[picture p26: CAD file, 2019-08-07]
M&A 2018/Hardware/Maxon Parts/Print/LRF Clamp.stl
12.0 x 1.50 x 32.0

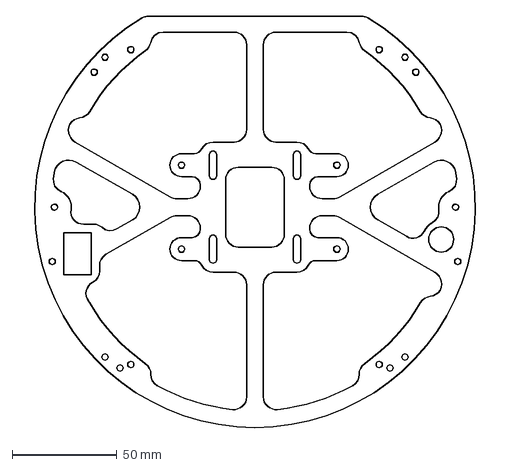
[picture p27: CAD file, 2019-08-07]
M&A 2018/Hardware/Maxon Parts/Top Plate.dxf
227.5 x 195.8 mm

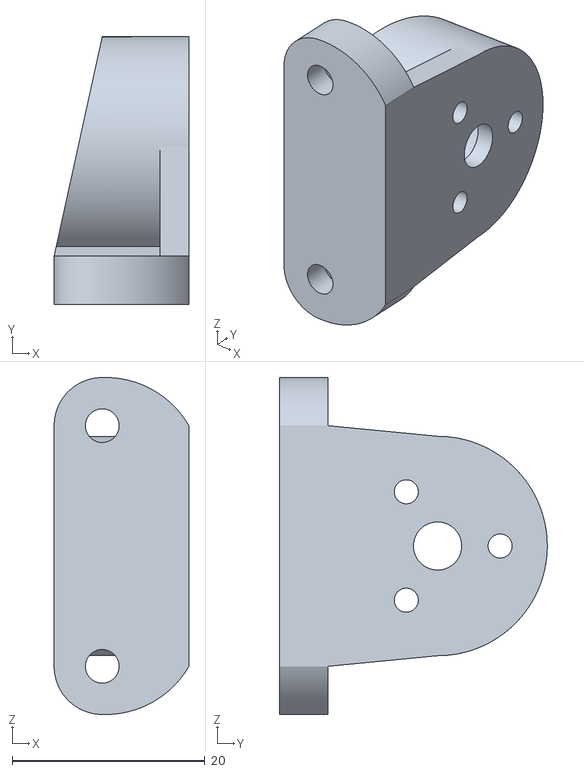
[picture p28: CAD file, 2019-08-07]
M&A 2018/Hardware/mk2/Imported Components/Maxon Mount/Maxon Mount2.stl
14.0 x 27.8 x 35.0

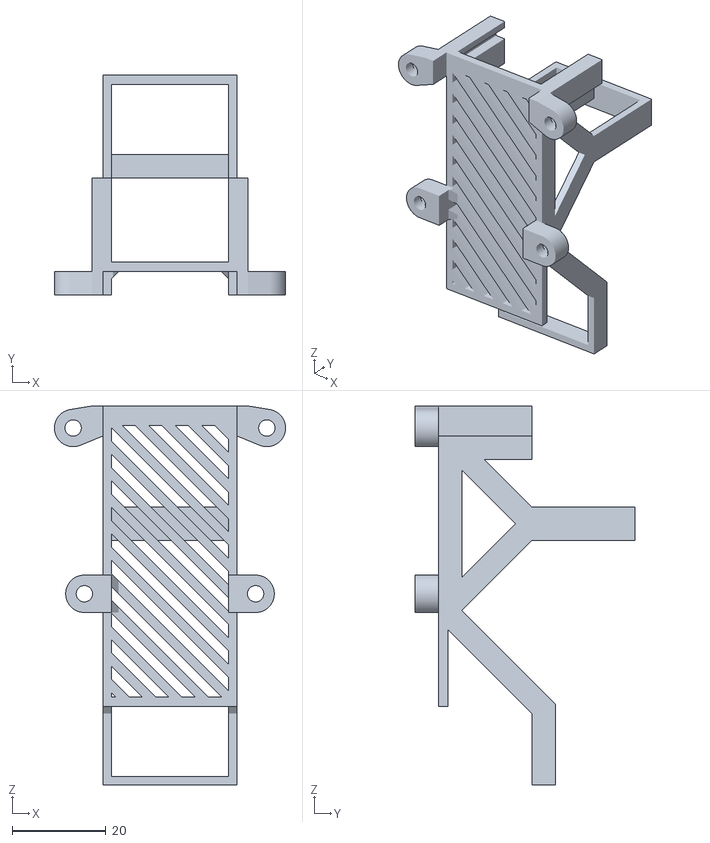
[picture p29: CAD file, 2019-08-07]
M&A 2019/Hardware/Design/Battery Case.stl
49.4 x 47.0 x 81.0

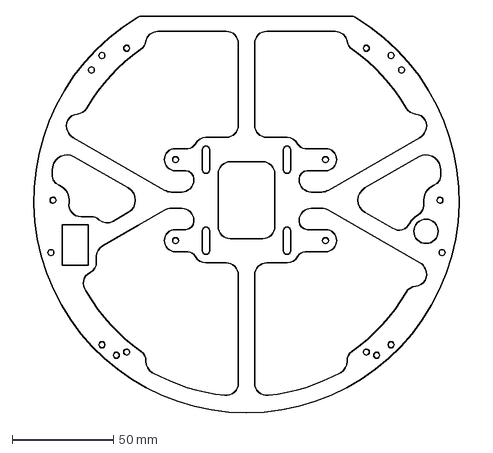
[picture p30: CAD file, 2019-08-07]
M&A 2018/Hardware/Maxon Parts/Laser Cut/Top Plate - 1.dxf
227.5 x 195.8 mm

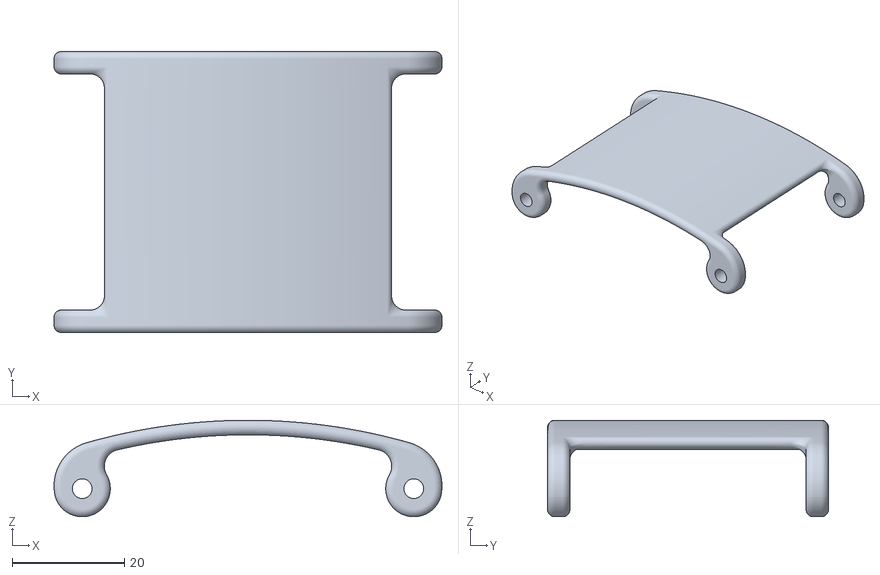
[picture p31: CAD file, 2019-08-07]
M&A 2018/Hardware/Maxon Parts/Print/Wheel Guard.stl
69.0 x 50.0 x 17.2

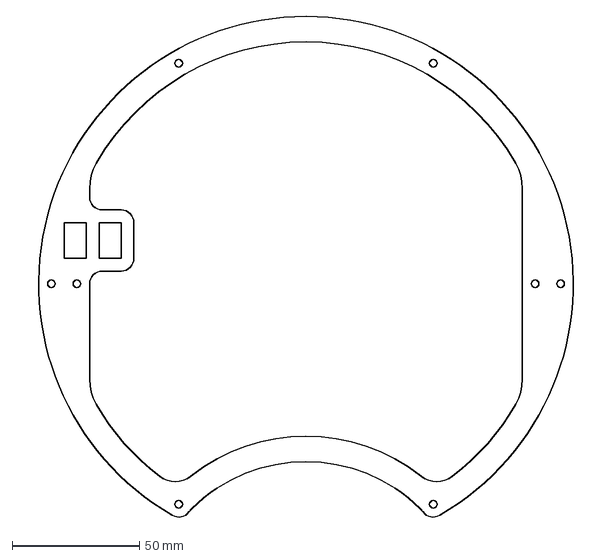
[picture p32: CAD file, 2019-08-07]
M&A 2019/Hardware/Design/Top Plate.dxf
227.4 x 197.2 mm

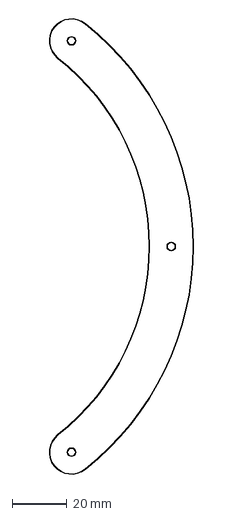
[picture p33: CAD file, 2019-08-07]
M&A 2018/Hardware/Maxon Parts/Laser Cut/Arc Handle - 12.dxf
53.4 x 168.0 mm

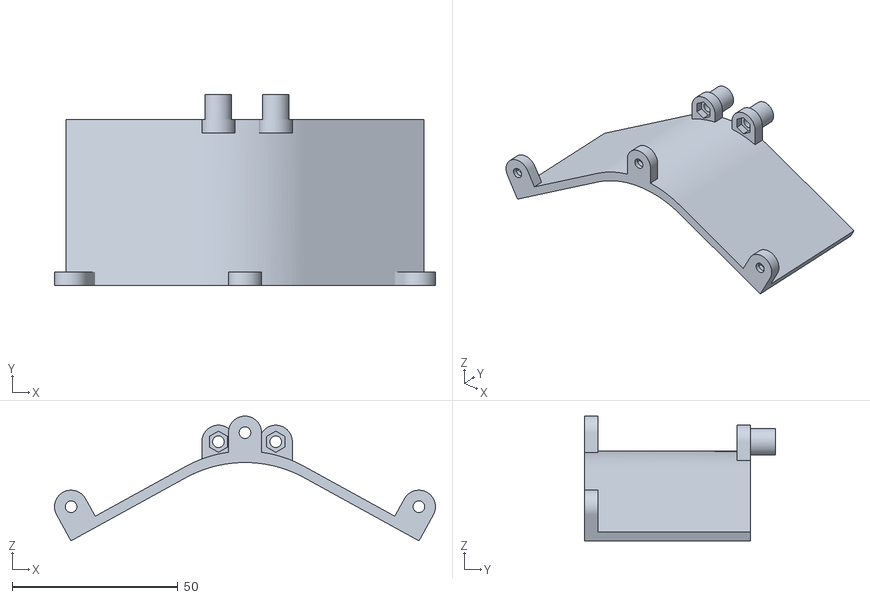
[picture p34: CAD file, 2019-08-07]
M&A 2018/Hardware/Maxon Parts/Print/Capture Zone.stl
114.8 x 57.5 x 37.6

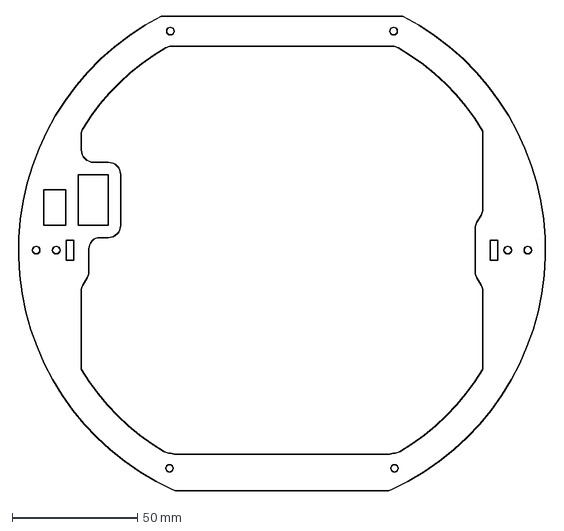
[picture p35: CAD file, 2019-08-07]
M&A 2019/Hardware/Design/Top Plate x 4 - Clear Polycarbonate.dxf
211.9 x 189.3 mm

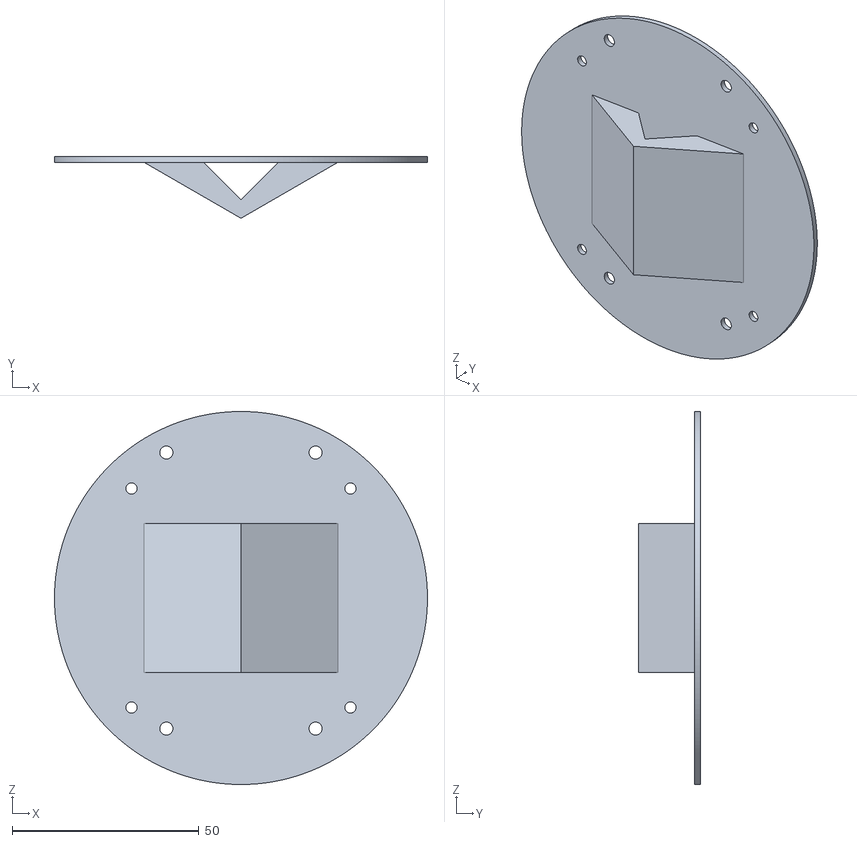
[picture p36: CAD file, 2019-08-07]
M&A 2018/Hardware/Maxon Parts/Print/Mirror Mount.stl
100.0 x 16.5 x 100.0

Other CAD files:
M&A 2019/Hardware/Design/Wire Jig Frame.stl
M&A 2018/Hardware/Maxon Parts/Print/LRF Mount.stl
M&A 2019/Hardware/Design/Bottom Plate.dxf
M&A 2018/Hardware/Maxon Parts/Print/Maxon Mount.stl
M&A 2018/Hardware/Maxon Parts/10mm Standoff.ipt
M&A 2018/Hardware/Maxon Parts/20mm Standoff.ipt
M&A 2018/Hardware/Maxon Parts/35.25mm Standoff.ipt
M&A 2018/Hardware/Maxon Parts/40mm Standoff.ipt
M&A 2018/Hardware/Maxon Parts/50mm Standoff.ipt
M&A 2018/Hardware/Maxon Parts/60mm Standoff.ipt
M&A 2018/Hardware/Maxon Parts/87.5mm Standoff (Matt Feros's conflicted copy 2018-11-11).ipt
M&A 2018/Hardware/Maxon Parts/87.5mm Standoff.ipt
M&A 2018/Hardware/Maxon Parts/87.5mm Standoff.newVer.ipt
M&A 2018/Hardware/Maxon Parts/Arc.ipt
M&A 2018/Hardware/Maxon Parts/Base Plate (Matt Feros's conflicted copy 2018-11-11).ipt
M&A 2018/Hardware/Maxon Parts/Base Plate.ipt
M&A 2018/Hardware/Maxon Parts/Capture Zone.ipt
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

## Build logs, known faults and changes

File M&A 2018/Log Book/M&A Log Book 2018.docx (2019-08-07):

M&A Logbook

By: Matthew Feros and

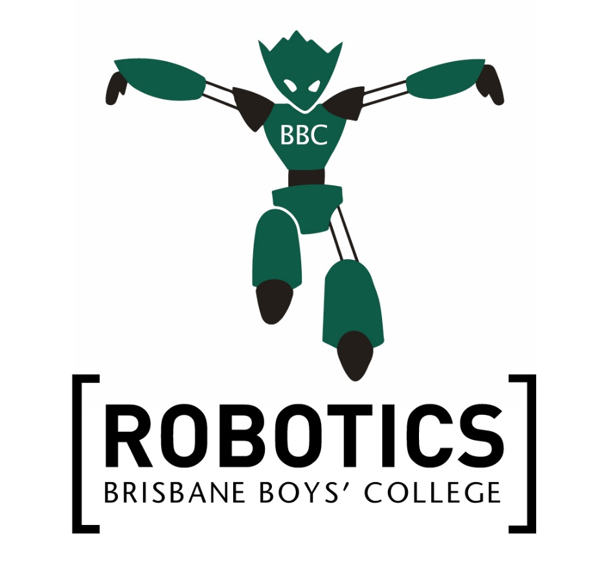
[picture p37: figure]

Aparaj Bogahawatta

# Project Overview

This year we need to create two robots that are able to play soccer against other robots. We are designing our robots from custom made parts, designed in Autodesk Inventor and Autodesk Eagle, and we are programming them in C++ by using the text editor, Atom. Our aim is to be able to program our robots so that they can play soccer with an IR emitting ball while adhering to all the rules of the RoboCup Junior Lightweight Competition. With these robots we would like to play as many games as possible in the regional, state and national competitions so we are able to improve our robot’s code and design for future years.

# Solving the Problem

This problem can be broken down into many parts. The two main parts in this project are the hardware side and the software side. In these separate components we need to break the problem even further so we both know what needs to be accomplished to fulfil the aim of this project.

## Hardware

In Hardware there are two main parts, the actual design and the electronic side. Our first job is to design a robot. This was done on Inventor. After we had finished that we had to make the electronic parts that was needed for the robot. The parts needed were the power supply, two motor controllers and a ring of IR sensors and a number of light sensors. The motor, controllers were the only off-the-shelf items that we used. All the other electronics parts were designed by Matthew Feros. We also decided to have a three plate design. This included a top, middle and bottom plate. The bottom plate would have the motors and the light sensors. The middle plate would hole the microcontroller, IR sensors, Power Supply and the motor controllers. The top plate would have the compass sensor and would act as a handle.

## Software

For the software side of the robot the first step was to find a text editor and a compiler that would work with C++ and the microcontroller. After we had finished that we needed to learn how to code in C++ and then we needed to decide how we were going to code our robot. We decided to break the software into smaller parts. Each part was for a different sensor. We made libraries which held the code for different sensors and then they were all combined into the main code where all the sensors would interact with eacc other so the robot could play a game of soccer.

# Roles of Team Members

The main role for Matthew Feros is the hardware part of the robot and the main role for Aparaj Bogahawatta is the software part of the robot. However, we both need to have knowledge in both areas since they both overlap. Aparaj needs to know how the robot is going to be designed so he is able to make a program accordingly. Matthew needs to make sure his design or any changes he makes does not interfere with the software side of the robot. Both members need to know how both areas work so that if there is an emergency in the competition any one of the team members can handle the situation. This means that both members need to have some knowledge in both fields to improve collaboration and results.

# Coding Platform

We are using a platform called Platformio. This is supplied by a company called GitHub. GitHub also supplied atom, which is a C++ editor. We downloaded atom because it is an easy-to-use textual-code editor and we used Platformio because it can be downloaded onto atom. However, we found that it was more efficient if we download Platformio through Python onto our computers because this meant we were able to use PowerShell on an app called GitBash to compile and upload our programs. The main reason for why we used Platformio is because it is efficient and really easy to learn.

# Hardware

## How are the robot parts arranged and why?

The robot consists of three main plates, a bottom plate, middle plate and the top plate. The bottom plate holds three motors and its controllers which are all angled 60° apart to allow for Omni-directional movement. This plate also holds light sensitive modules which give the robot sight as to the colour of the surface under the robot. This allows the robot to avoid the outlines of the field, which if passed will have the robot removed from the field. The middle plate consists of holes to accommodate 12 infrared light sensitive modules, the main controller and the inbuilt power supply. The top plate houses the direction sensitive module to give the robot information as to what side of the field it is facing, the top plate also protects the electronics under it, allows for a handle to be mounted to the top and stops the robot from entering the goal.

## Where are the motors?

The motors are orientated at 60° apart from each other around the centre of the robot. The motors have omnidirectional wheels attached to their shafts that allow for controlled movement in the perpendicular direction of the robot however the wheels move freely in the other direction. The motors are held by custom made 3D printed mounts that are connected to the bottom and middle platesunts on the bottom plate of the robot so that they are low enough to maintain contact with the field.

## What do they do?

The motors give accurate control over the movement of the robot. Their speeds are dynamically controlled by a motor controller which uses a 12 volt current and a PWM signal from the Teensy microcontroller to move the motors at a controlled speed. They allow us to move our robot so we are able to orbit and follow the IR emitting ball.

## Where are the sensors?

There are four different types of sensors on our robot. There are light sensors, TSSP Sensors, an IMU sensor and a Laser Range Finder (LRF). The light sensors are located on the bottom of the robot. The TSSP Sensors are located in the middle plate of the robot. The IMU is on the very top of the robot and is in the centre of the robot. The LRF is located at the back of the top plate

## What do they do?

Light Sensors are placed in a ring so the robot can easily detect colours in all direction. They detect the different colours of the playing field allowing the robot to detect the out-line and avoid the out area. The TSSP sensors are the sensors that detect the Infrared Ball. They are placed at 30o increments so the ball can be seen in all directions. The IMU sensor is an accelerometer, magnetometer and gyro sensors all in one PCB. We only use the Gyroscope sensor because that can sense direction. This means that we are able to keep our robots facing in one direction all the time. The LRF allows us to see the distance the sensor is away from another object. This is useful for a goalie.

## How do you keep it from breaking?

We keep the sensors from breaking by having plates that protect them. For the light sensors, the bottom plate surrounds the light sensors meaning that any impact will be absorbed by the base plate rather than the sensors. The same is for the TSSP sensors. They are surrounded by the Middle plate, meaning that any impacts will also be absorbed by the middle plate. The LRF is the only sensor that has more of a chance of being broken. However, it is still just inside the top plate meaning it would be difficult for another robot to break it.

## Is it safe to use around people?

The robot is safe to use around people because it is a cylindrical shape with rounded corners. There are also wheel guards that cover the wheels, meaning that the fast spinning motors will not hurt anyone’s fingers. The robot is very fast meaning that it could hurt someone who puts their hand inside the robot, but if the right safety precautions are taken there should be no injuries.

# Software

## What software did you use and why?

We are using a text editor called Atom to edit our code. We use Atom because we are able to download a platform called Platformio through it. Using Platformio we are able to make a code for a specific microcontroller. We just have to put in the name of the microcontroller and if Platformio have information about it, it will create a project that will be compatible with the microcontroller. We also used Atom because we were able to use a C++ editor on that software.

## Pseudo Code

Set-Up Code

The Arduino is turned on.

All the sensors are powered and run through their respective setup codes.

The motors are setup and are braked.

The Arduino checks if it has to act as a Defender or an Attacker.

Loop

The robot uses the different values from the IR, Light, Gyroscope and LRF sensors to know where the ball is and what direction to move. The light sensors are for out avoidance. The IR sensors detect the ball. The compass sensor makes sure the robot is always facing in the same direction. The LRF detects the distance from the goal.

## Can you show how your program evolved?

Our code has evolved throughout the past year. It started as a logic code. This is where all the different calculations were put. The syntax wasn’t adhered to but all the mathematical calculations that would be used later on were all in that code. This meant when I was writing my code I was able to refer back to the logic code for all the calculations. The next big change was for an actual code. This code adhered to the syntax and it was designed so it was able to be compiled and uploaded into an Arduino Mega. This code took much longer to write and edit because I had to make libraries for all the different objects and then bring them together in the main code. The next big change was the competition code. This code had a striker program as well as a goalie program. It was also much more efficient and relied on more pre-processed variables rather than normal variables. After using that code for the state competition, I moved to a much more object orientated program. This program followed the normal Standards of C++. This meant that the readability was better and it would be easier to identify different parts of the code.

# Electronics

## What modules did you use and why?

We used _______ as motor controllers. We used motor controllers so that we were able to control the speed of each motor, thus controlling the direction of which the robot is moving. We used TSSP, Light and IMU sensors to detect the direction of the ball, detect the out-line and to detect the heading of the robot. We also use an LRF for our goalie to detect the distance from the goal. All this data helps the robot to run efficiently and smoothly so that it can play a proper game of soccer. We used a Teensy 3.5 as the microcontroller because they are pre-made and they have the ability to run the robot to a standard needed to power all the components.

## Did you use custom electronics?

We did use custom electronics for the Power circuit, Teensy3.5s, Light and TSSP sensors. We designed the circuitry on an app called Autodesk Eagle and then we ordered them through a company called PCB Way.

## Did you make your own circuits?

We did make our own circuits because we were only allowed to make individual components with Eagle rather than the whole robot. This meant that instead of one massive PCB we had multiple smaller ones that were all connected in a massive circuit.

# Community Outreach

We will be showcasing our robots to the community and some teachers and peers on Robocup competition days. We do not have any specific dates to show off our robots other than the competition however, our school does Open Mornings where our robots will be displayed for others to see.

# What was the hardest part of the Project?

## Aparaj Bogahawatta:

### What challenges did the project face?

The hardest part of the project was switching to the Teensy 3.5s. This is because I had to rewrite my whole code so that it was more efficient and so that it would work for our new robots. Another hard part was creating a defender from scratch.

### The team?

There was no challenges with the team since we were able to work well together and we always had jobs to do and were never not doing anything useful.

### The software?

The hardest part about the software was trying to get our TSSPs to read faster than 20 times a second. After this was achieved, the whole program was a lot more efficient and worked very well.

### The implementation?

### Choosing a colour scheme?

### How did you go about fixing them?

### How would you improve the whole process?

### What’s next?

## Matthew Feros:

### What challenges did the project face?

### The team?

### The design?

### The implementation?

### Choosing a colour scheme?

### How did you go about fixing them?

### How would you improve the whole process?

### What’s next?

Note: Fill this out the week before nationals.

# The innovative parts of the robot?

## Why is the robot really cool :)?

We are the first team in BBC Robotics to be using custom PCBs in our first year of Custom Soccer. This means that we had to design all our PCBs from scratch. We also have a capture zone that is curved to the shape of the ball so the ball doesn’t come out of the capture zone as easily. We are also the first team in Australia to use a V shaped mirror on our robot. This means that we are able to see in two directions with only one camera. We also have curved guards over our wheels so they are completely covered and don’t get damaged by other robots. These guards match with the colour scheme of the robot. We have made the robot so that one of the robots is mainly black and the other is mainly white.

# Weekly Log Book

## Term 1:

### Week 6:

#### Aparaj:

This week I solved the problem with my Arduino Mega. I was able to connect my Mega to my computer and I knew why it was connecting before. I had my code automatically sending the code on a different COM link to the one my Mega was connected to. This meant I had to change the COM link on my code and now it uploads and monitors perfectly. I also tested my TSOP array library for direction testing. I made sure that if I inputted an angle it would return the same angle after multiple calculations.

#### Matthew:

### Week 7:

#### Aparaj:

This week I put to use my Mega as it was now able to connect to my computer. I was able to test my orbit angles and strength readings using the Serial Monitor on PowerShell. I found however that my compass correction calculations are messing up my motor calculations. Next week I will have to learn how to fix this problem and understand my compass code better.

#### Matthew:

### Week 8:

#### Aparaj:

This week I learnt how the I2C and Compass library files work and I understood why my motor calculations were not working. I also made a robot library and a pixy library. The robot library has all the calculations that I had in the main but it is now under the robot object. I also made a Pixy library just in case we are allowed to use pixies. This meant that I made the code to adjust the rotations in my robot library. Next week I have got to test that the pixy code works and double check that the compass correction works correctly.

#### Matthew:

### Week 9:

#### Aparaj:

I tested my pixy code this week and my compass correction code. All of the logic works perfectly. However, I need a Gyroscope to make sure that my compass code works 100% correctly. I learnt how to solder and I soldered some capacitors on some light sensors. I would not be doing most of the soldering because that is not my part of the team, however, I would need to help when needed or when I had nothing else to do so that we would have more time to test with a robot.

#### Matthew:

### Week 10:

#### Aparaj:

This week I just helped out with some soldering again as I am not able to do anything without a physical robot. There was only one session of robotics this week meaning less work was done.

#### Matthew:

### Holiday Week 1:

#### Aparaj:

I was away for a holiday during this week.

#### Matthew:

### Holiday Week 2:

#### Aparaj:

I was away for a holiday during this week.

#### Matthew:

## Term 2:

### Week 1:

#### Aparaj:

This week I learnt about how to program a Pixy. A Pixy is a camera that can be used to track the whereabouts of the goal. This means that our robot will score even more goals. I made a function that would return the angle of where the goal is. I also found a few variables that are able to be pre-processed. I changed these variables to constants so the program would be more efficient. I also started a Goalie library. This is so that we are able to have a goalie in competition if we are able to pull it off.

#### Matthew:

### Week 2:

#### Aparaj:

This week I finished off my Goalie library. It compiled and seemed to work, however I wasn’t able to test it yet. I tried to make the program by using trigonometry, but I found out that it was much easier to use the object angle from the camera to calculate the distance the robot was from the goal. I also found out that my Pixy wasn’t connecting to my computer for some reason.

#### Matthew:

### Week 3:

#### Aparaj:

This week I tested our power circuits. They all worked properly. The means that we had five working power circuits. I also designed a draft logo for our team. I was able to fix up some minor errors in the program. I also made a barrier between the different objects’ variables. This means that other objects can’t change the value of variable from other objects. I also finished testing our compass correction code on the test robot and all of it worked fine in the Serial mode. However, the robot wasn’t working on the field and we weren’t sure why.

#### Matthew:

### Week 4:

#### Aparaj:

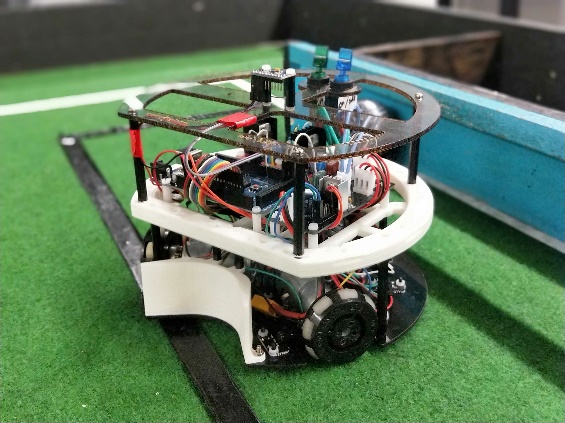
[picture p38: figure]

This week we found out that one of the motor controllers was not working. That is why the compass correction was messing up. I replaced the motor controllers and our robot is working well. I am now trying to fine tune the compass correction by using the PID method. I found that I could also improve the efficiency of the code by having different classes already defined after the creation of one object. I also identified a problem in the code. Sometimes the motors would stop moving even when it was supposed to be compass correcting. I fixed the problem by using PID to calculate my compass correction. Before I was just using P but I wasn’t doing the calculations correctly. I fixed the calculation and now the robot works. I just have to fine tune the correction. I have also added a program that negates the compass drift by calculating the change per second and adding that on. We got our plates and we built one of the robots but the TSOP ring was not the latest one. This meant that the standoffs we leaning out a little bit for the top plate.

#### Matthew:

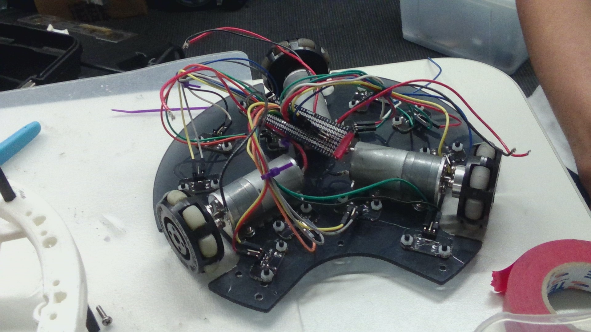
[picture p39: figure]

### Week 5:

#### Aparaj:

This week I started to test the compass correction on our actual robot. I found that our proportional and derivative was going to be very high due to the fact that our motors were very weak. However, I soon realised that I was able to have a minimum correcting speed so I could bring my derivative and proportional values back down to normal. I also started to work on my out avoidance. I found out that my light sensors were returning weird values. However, all the values were consistent between the light sensors so it was possible to program them. I also added a function in my program that would negate the drift of our Gyroscope sensor. This meant that the readings of the gyroscope were much more accurate.

#### Matthew:

### Week 6:

#### Aparaj:

This week I found that the motors we were using were all running at different speeds and they were making the compass correction inaccurate. The motors were also clogging up, this meant that sometimes one of the motors needed replacing. This meant that I had to wait for Matthew to switch the motors so I was able to code them.

#### Matthew:

### Week 7:

#### Aparaj:

This week I started to started to work with the compass correction. We had new motors on our robot. However, I found that the new motors didn’t have enough talk to actually move the robot on the field. This meant the motors weren’t able to move the robot unless they were at a very high speed. This meant that there was a problem with the motor. However, I was able to check my compass correction code with my Serial Monitor and the Compass. At the end of the week we found that one of our motors was only spinning in one direction. This meant that when it was supposed to be spinning one way it would just not spin. When it needed to spin the other way it would work fine.

#### Matthew:

### Week 8:

#### Aparaj:

This week I found out that the PWM pins were not in the right places on the robot. After fixing this, all the motors starting spinning in the correct direction. Then I started to work on the TSOPs. I found out that two of the TSOPs were broken. This meant that they needed to be replaced. I managed to get the robot to go towards the direction of the ball. Then the next step was to orbit the ball. I found out that the orbit was not large enough. This meant that the robot kept running into the ball. I also found out that sometimes the robot would just crash for no reason. The reason was because the compass sensor was not connected properly to the Arduino and this was stopping the whole code.

Aparaj Bogahawatta and Matthew Feros1529/09/2018

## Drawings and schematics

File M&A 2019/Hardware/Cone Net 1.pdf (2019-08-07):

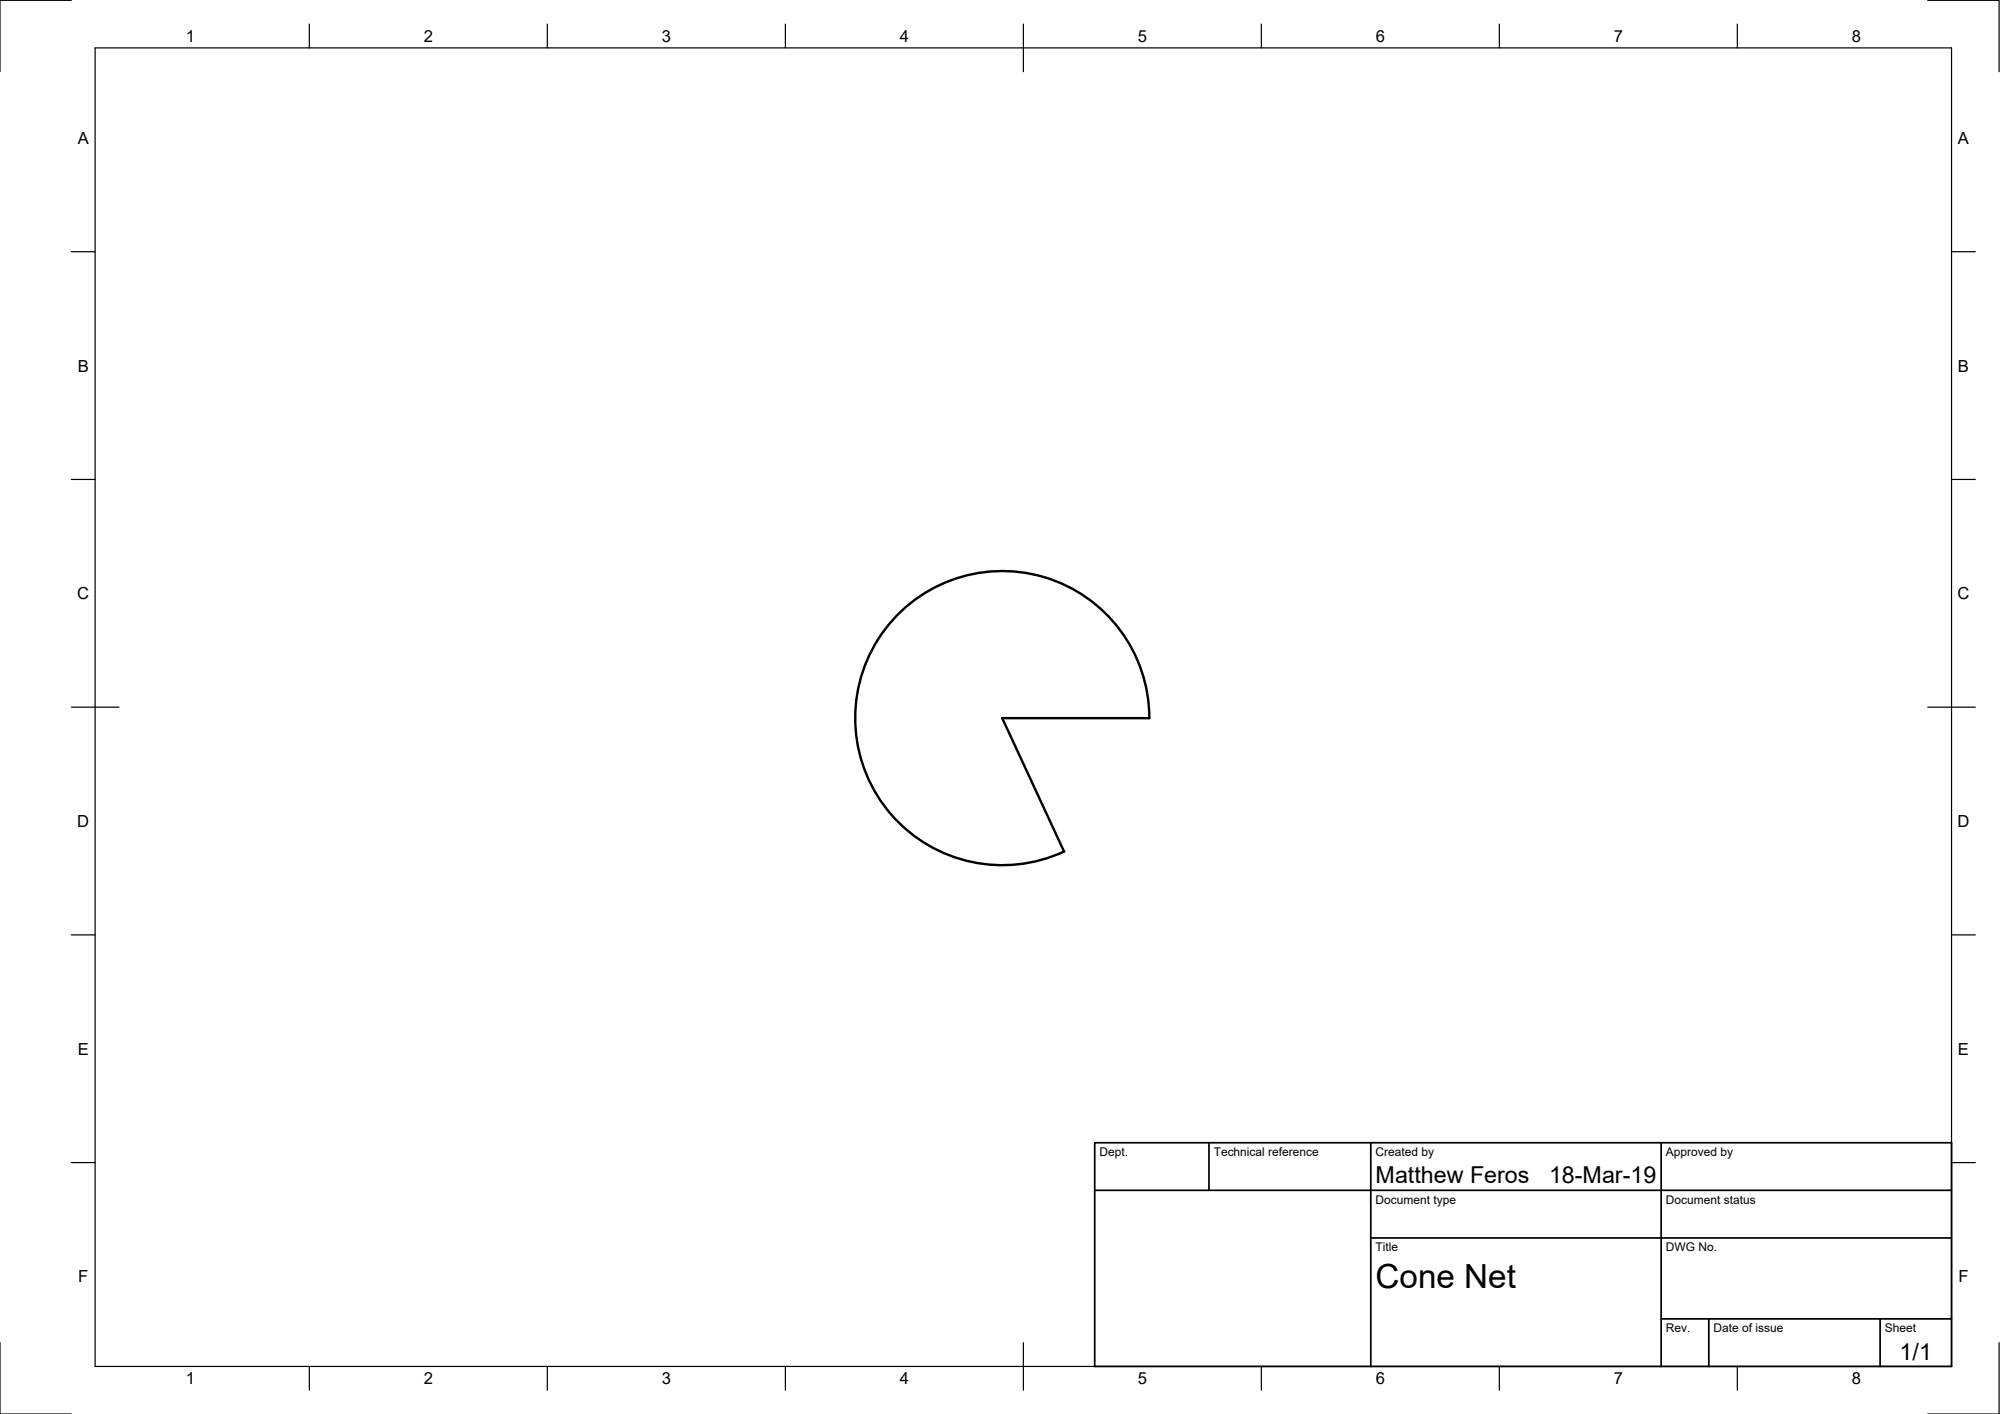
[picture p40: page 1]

Dept. | Technical reference | Created by Matthew Feros 18-Mar-19 | Approved by

Document type | Document status

Title Cone Net | DWG No.

Rev. | Date of issue | Sheet 1/1

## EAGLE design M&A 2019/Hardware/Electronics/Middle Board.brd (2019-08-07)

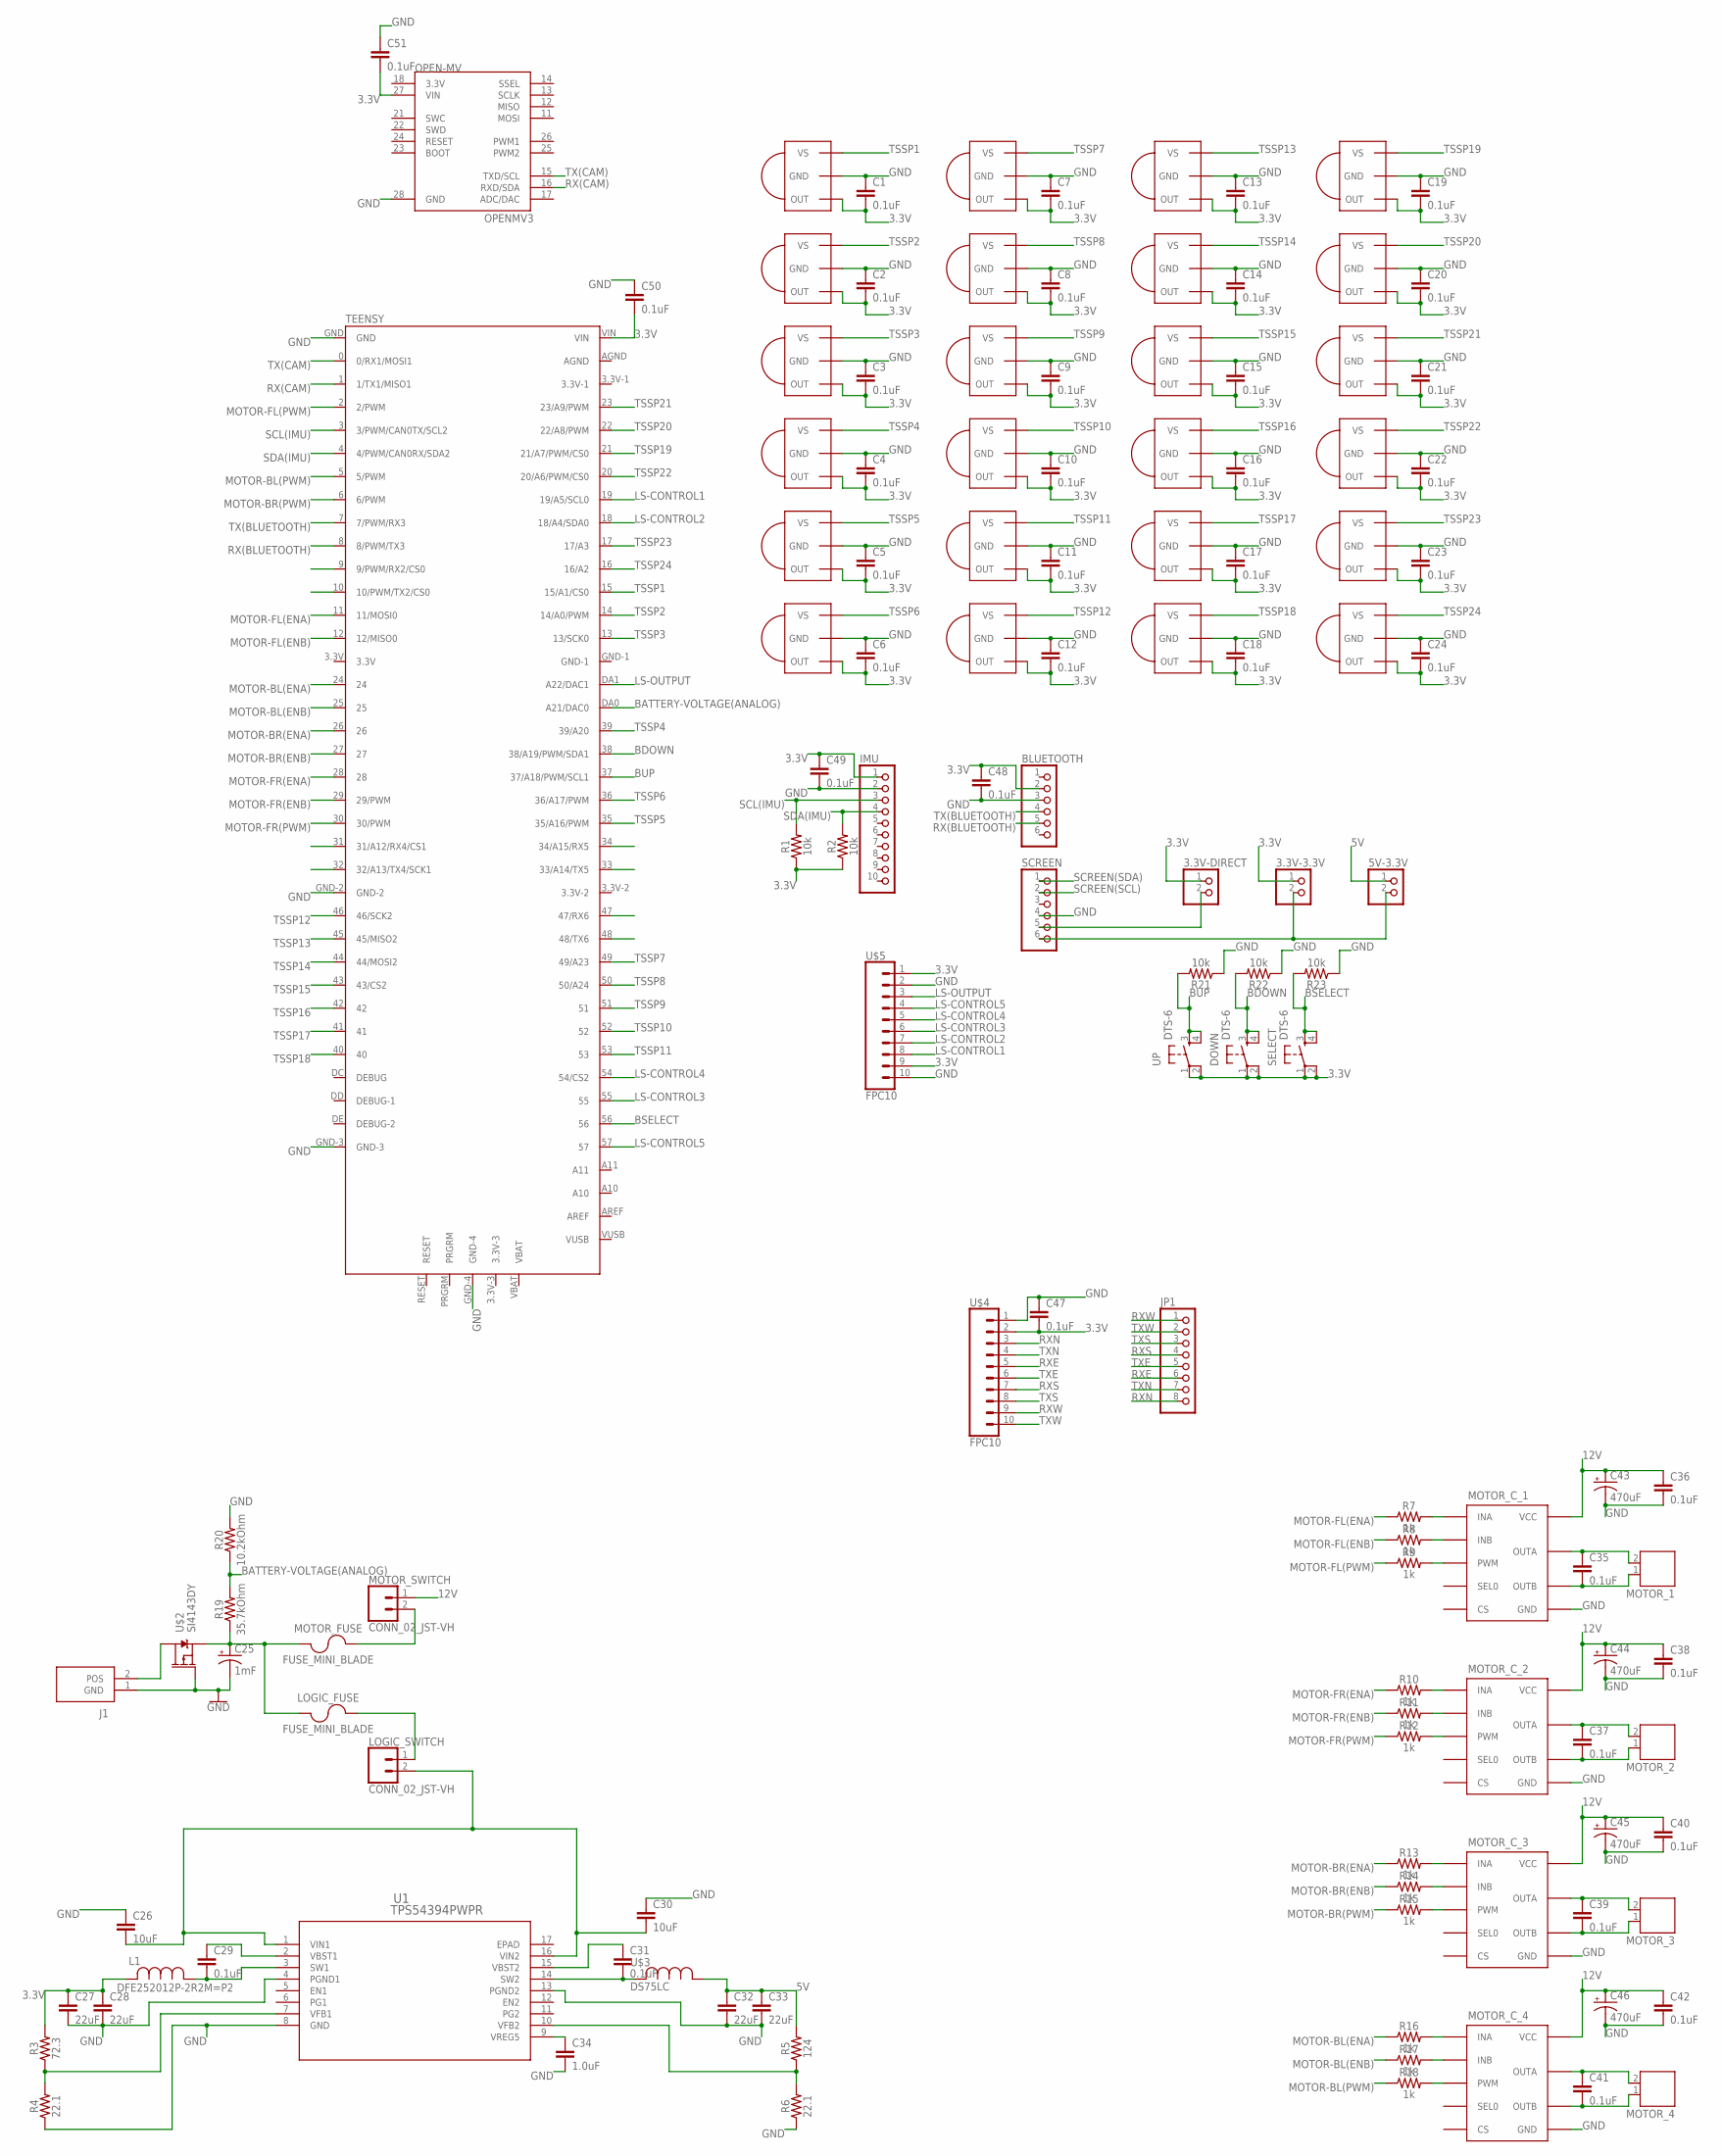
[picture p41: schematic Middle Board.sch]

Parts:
3.3V-3.3V, 3.3V-DIRECT, 5V-3.3V: PINHD-1X2; 1X02
BLUETOOTH: PINHD-1X6; 1X06
C1, C2, C3, C4, C5, C6, C7, C8, C9, C10, C11, C12, C13, C14, C15, C16, C17, C18, C19, C20, C21, C22, C23, C24, C29, C31, C35, C36, C37, C38, C39, C40, C41, C42, C47, C48, C49, C50, C51: 0.1uF; 0603
C25: 1mF; CPOL-RADIAL-5MM-10MM
C26, C30: 10uF; 0805
C27, C28, C32, C33: 22uF; 0805
C34: 1.0uF; 0805
C43, C44, C45, C46: 470uF; E3,5-8
DOWN: DTS-6
IMU: PINHD-1X10; 1X10
J1: PRT-10474; SHDR2W320P716_1X2_1574X813X158
JP1: PINHD-1X8; 1X08
L1: DFE252012P-2R2M=P2; DFE252012P-1R0M=P2
LOGIC_FUSE: FUSE_MINI_BLADE; SL-1538
LOGIC_SWITCH: CONN_02_JST-VH; B2P-VH
MOTOR_1, MOTOR_2, MOTOR_3, MOTOR_4: JST-PH2
MOTOR_C_1, MOTOR_C_2, MOTOR_C_3, MOTOR_C_4: VNH7100BASTR; SO-16
MOTOR_FUSE: FUSE_MINI_BLADE; SL-1538
MOTOR_SWITCH: CONN_02_JST-VH; B2P-VH
OPEN-MV: OPENMV3
R1, R2, R21, R22, R23: 10k; 0603
R3: 72.3; 0603
R4, R6: 22.1; 0603
R5: 124; 0603
R7, R8, R9, R10, R11, R12, R13, R14, R15, R16, R17, R18: 1k; 0603
R19: 35.7kOhm; 0603
R20: 10.2kOhm; 0603
SCREEN: PINHD-1X6; 1X06
SELECT: DTS-6
TEENSY: TEENSY-3.5
TSSP1, TSSP2, TSSP3, TSSP4, TSSP5, TSSP6, TSSP7, TSSP8, TSSP9, TSSP10, TSSP11, TSSP12, TSSP13, TSSP14, TSSP15, TSSP16, TSSP17, TSSP18, TSSP19, TSSP20, TSSP21, TSSP22, TSSP23, TSSP24: TSSP58038; MINICAST
U1: TPS54394PWPR; PWP16_3P4X2P46
U$2: SI4143DY; SO-8
U$3: DS75LC
U$4, U$5: FPC10
UP: DTS-6

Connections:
3.3V: 3.3V-3.3V.1, 3.3V-DIRECT.1, BLUETOOTH.2, C1.2, C2.2, C3.2, C4.2, C5.2, C6.2, C7.2, C8.2, C9.2, C10.2, C11.2, C12.2, C13.2, C14.2, C15.2, C16.2, C17.2, C18.2, C19.2, C20.2, C21.2, C22.2, C23.2, C24.2, C27.1, C28.1, C47.2, C48.1, C49.1, C50.2, C51.2, DOWN.1, DOWN.2, IMU.1, L1.2, OPEN-MV.27 (VIN), R1.1, R2.1, R3.2, SELECT.1, SELECT.2, TEENSY.VIN, TSSP1.1 (OUT), TSSP2.1 (OUT), TSSP3.1 (OUT), TSSP4.1 (OUT), TSSP5.1 (OUT), TSSP6.1 (OUT), TSSP7.1 (OUT), TSSP8.1 (OUT), TSSP9.1 (OUT), TSSP10.1 (OUT), TSSP11.1 (OUT), TSSP12.1 (OUT), TSSP13.1 (OUT), TSSP14.1 (OUT), TSSP15.1 (OUT), TSSP16.1 (OUT), TSSP17.1 (OUT), TSSP18.1 (OUT), TSSP19.1 (OUT), TSSP20.1 (OUT), TSSP21.1 (OUT), TSSP22.1 (OUT), TSSP23.1 (OUT), TSSP24.1 (OUT), U$4.2, U$5.1, U$5.9, UP.1, UP.2
5V: 5V-3.3V.1, C32.1, C33.1, R5.2, U$3.P$1 (1)
12V: C36.1, C38.1, C40.1, C42.1, C43.+, C44.+, C45.+, C46.+, MOTOR_C_1.4 (VCC), MOTOR_C_1.5 (VCC), MOTOR_C_1.12 (VCC), MOTOR_C_2.4 (VCC), MOTOR_C_2.5 (VCC), MOTOR_C_2.12 (VCC), MOTOR_C_3.4 (VCC), MOTOR_C_3.5 (VCC), MOTOR_C_3.12 (VCC), MOTOR_C_4.4 (VCC), MOTOR_C_4.5 (VCC), MOTOR_C_4.12 (VCC), MOTOR_SWITCH.1
BATTERY-VOLTAGE(ANALOG): R19.2, R20.1, TEENSY.DA0 (A21/DAC0)
BDOWN: DOWN.3, DOWN.4, R22.2, TEENSY.38 (38/A19/PWM/SDA1)
BSELECT: R23.2, SELECT.3, SELECT.4, TEENSY.56
BUP: R21.2, TEENSY.37 (37/A18/PWM/SCL1), UP.3, UP.4
GND: BLUETOOTH.3, C1.1, C2.1, C3.1, C4.1, C5.1, C6.1, C7.1, C8.1, C9.1, C10.1, C11.1, C12.1, C13.1, C14.1, C15.1, C16.1, C17.1, C18.1, C19.1, C20.1, C21.1, C22.1, C23.1, C24.1, C25.-, C26.1, C27.2, C28.2, C30.1, C32.2, C33.2, C34.2, C36.2, C38.2, C40.2, C42.2, C43.-, C44.-, C45.-, C46.-, C47.1, C48.2, C49.2, C50.1, C51.1, IMU.2, J1.1 (GND), MOTOR_C_1.1 (GND), MOTOR_C_1.8 (GND), MOTOR_C_1.9 (GND), MOTOR_C_1.16 (GND), MOTOR_C_2.1 (GND), MOTOR_C_2.8 (GND), MOTOR_C_2.9 (GND), MOTOR_C_2.16 (GND), MOTOR_C_3.1 (GND), MOTOR_C_3.8 (GND), MOTOR_C_3.9 (GND), MOTOR_C_3.16 (GND), MOTOR_C_4.1 (GND), MOTOR_C_4.8 (GND), MOTOR_C_4.9 (GND), MOTOR_C_4.16 (GND), OPEN-MV.28 (GND), R4.1, R6.1, R20.2, R21.1, R22.1, R23.1, SCREEN.4, TEENSY.GND, TEENSY.GND-2, TEENSY.GND-3, TEENSY.GND-4, TSSP1.2 (GND), TSSP2.2 (GND), TSSP3.2 (GND), TSSP4.2 (GND), TSSP5.2 (GND), TSSP6.2 (GND), TSSP7.2 (GND), TSSP8.2 (GND), TSSP9.2 (GND), TSSP10.2 (GND), TSSP11.2 (GND), TSSP12.2 (GND), TSSP13.2 (GND), TSSP14.2 (GND), TSSP15.2 (GND), TSSP16.2 (GND), TSSP17.2 (GND), TSSP18.2 (GND), TSSP19.2 (GND), TSSP20.2 (GND), TSSP21.2 (GND), TSSP22.2 (GND), TSSP23.2 (GND), TSSP24.2 (GND), U1.4 (PGND1), U1.8 (GND), U1.13 (PGND2), U$2.4 (G), U$4.1, U$5.2, U$5.10
LS-CONTROL1: TEENSY.19 (19/A5/SCL0), U$5.8
LS-CONTROL2: TEENSY.18 (18/A4/SDA0), U$5.7
LS-CONTROL3: TEENSY.55, U$5.6
LS-CONTROL4: TEENSY.54 (54/CS2), U$5.5
LS-CONTROL5: TEENSY.57, U$5.4
LS-OUTPUT: TEENSY.DA1 (A22/DAC1), U$5.3
MOTOR-BL(ENA): R16.1, TEENSY.24
MOTOR-BL(ENB): R17.1, TEENSY.25
MOTOR-BL(PWM): R18.1, TEENSY.5 (5/PWM)
MOTOR-BR(ENA): R13.1, TEENSY.26
MOTOR-BR(ENB): R14.1, TEENSY.27
MOTOR-BR(PWM): R15.1, TEENSY.6 (6/PWM)
MOTOR-FL(ENA): R7.1, TEENSY.11 (11/MOSI0)
MOTOR-FL(ENB): R8.1, TEENSY.12 (12/MISO0)
MOTOR-FL(PWM): R9.1, TEENSY.2 (2/PWM)
MOTOR-FR(ENA): R10.1, TEENSY.28
MOTOR-FR(ENB): R11.1, TEENSY.29 (29/PWM)
MOTOR-FR(PWM): R12.1, TEENSY.30 (30/PWM)
unnamed: J1.2 (POS), U$2.5 (D), U$2.6 (D), U$2.7 (D), U$2.8 (D)
unnamed: MOTOR_FUSE.P$2 (2), MOTOR_SWITCH.2
unnamed: C25.+, LOGIC_FUSE.P$1 (1), MOTOR_FUSE.P$1 (1), R19.1, U$2.1 (S), U$2.2 (S), U$2.3 (S)
unnamed: LOGIC_FUSE.P$2 (2), LOGIC_SWITCH.1
unnamed: MOTOR_C_1.3 (INA), R7.2
unnamed: C29.1, U1.2 (VBST1)
unnamed: C29.2, L1.1, U1.3 (SW1)
unnamed: C31.1, U1.15 (VBST2)
unnamed: R3.1, R4.2, U1.7 (VFB1)
unnamed: C31.2, U1.14 (SW2), U$3.P$2 (2)
unnamed: C34.1, U1.9 (VREG5)
unnamed: MOTOR_C_1.6 (INB), R8.2
unnamed: C26.2, C30.2, LOGIC_SWITCH.2, U1.1 (VIN1), U1.16 (VIN2)
unnamed: R5.1, R6.2, U1.10 (VFB2)
unnamed: MOTOR_C_1.11 (PWM), R9.2
unnamed: C35.1, MOTOR_1.2, MOTOR_C_1.2 (OUTA), MOTOR_C_1.15 (OUTA)
unnamed: C35.2, MOTOR_1.1, MOTOR_C_1.7 (OUTB), MOTOR_C_1.10 (OUTB)
unnamed: MOTOR_C_2.3 (INA), R10.2
unnamed: MOTOR_C_2.6 (INB), R11.2
unnamed: MOTOR_C_2.11 (PWM), R12.2
unnamed: C37.1, MOTOR_2.2, MOTOR_C_2.2 (OUTA), MOTOR_C_2.15 (OUTA)
unnamed: C37.2, MOTOR_2.1, MOTOR_C_2.7 (OUTB), MOTOR_C_2.10 (OUTB)
unnamed: MOTOR_C_3.3 (INA), R13.2
unnamed: MOTOR_C_3.6 (INB), R14.2
unnamed: MOTOR_C_3.11 (PWM), R15.2
unnamed: C39.1, MOTOR_3.2, MOTOR_C_3.2 (OUTA), MOTOR_C_3.15 (OUTA)
unnamed: C39.2, MOTOR_3.1, MOTOR_C_3.7 (OUTB), MOTOR_C_3.10 (OUTB)
unnamed: MOTOR_C_4.3 (INA), R16.2
unnamed: MOTOR_C_4.6 (INB), R17.2
unnamed: MOTOR_C_4.11 (PWM), R18.2
unnamed: C41.1, MOTOR_4.2, MOTOR_C_4.2 (OUTA), MOTOR_C_4.15 (OUTA)
unnamed: C41.2, MOTOR_4.1, MOTOR_C_4.7 (OUTB), MOTOR_C_4.10 (OUTB)
unnamed: 3.3V-DIRECT.2, SCREEN.5
unnamed: 3.3V-3.3V.2, 5V-3.3V.2, SCREEN.6
RX(BLUETOOTH): BLUETOOTH.5, TEENSY.8 (8/PWM/TX3)
RX(CAM): OPEN-MV.16 (RXD/SDA), TEENSY.1 (1/TX1/MISO1)
RXE: JP1.6, U$4.5
RXN: JP1.8, U$4.3
RXS: JP1.4, U$4.7
RXW: JP1.1, U$4.9
SCL(IMU): IMU.3, R1.2, TEENSY.3 (3/PWM/CAN0TX/SCL2)
SCREEN(SCL): SCREEN.2
SCREEN(SDA): SCREEN.1
SDA(IMU): IMU.4, R2.2, TEENSY.4 (4/PWM/CAN0RX/SDA2)
TSSP1: TEENSY.15 (15/A1/CS0), TSSP1.3 (VS)
TSSP2: TEENSY.14 (14/A0/PWM), TSSP2.3 (VS)
TSSP3: TEENSY.13 (13/SCK0), TSSP3.3 (VS)
TSSP4: TEENSY.39 (39/A20), TSSP4.3 (VS)
TSSP5: TEENSY.35 (35/A16/PWM), TSSP5.3 (VS)
TSSP6: TEENSY.36 (36/A17/PWM), TSSP6.3 (VS)
TSSP7: TEENSY.49 (49/A23), TSSP7.3 (VS)
TSSP8: TEENSY.50 (50/A24), TSSP8.3 (VS)
TSSP9: TEENSY.51, TSSP9.3 (VS)
TSSP10: TEENSY.52, TSSP10.3 (VS)
TSSP11: TEENSY.53, TSSP11.3 (VS)
TSSP12: TEENSY.46 (46/SCK2), TSSP12.3 (VS)
TSSP13: TEENSY.45 (45/MISO2), TSSP13.3 (VS)
TSSP14: TEENSY.44 (44/MOSI2), TSSP14.3 (VS)
TSSP15: TEENSY.43 (43/CS2), TSSP15.3 (VS)
TSSP16: TEENSY.42, TSSP16.3 (VS)
TSSP17: TEENSY.41, TSSP17.3 (VS)
TSSP18: TEENSY.40, TSSP18.3 (VS)
TSSP19: TEENSY.21 (21/A7/PWM/CS0), TSSP19.3 (VS)
TSSP20: TEENSY.22 (22/A8/PWM), TSSP20.3 (VS)
TSSP21: TEENSY.23 (23/A9/PWM), TSSP21.3 (VS)
TSSP22: TEENSY.20 (20/A6/PWM/CS0), TSSP22.3 (VS)
TSSP23: TEENSY.17 (17/A3), TSSP23.3 (VS)
TSSP24: TEENSY.16 (16/A2), TSSP24.3 (VS)
TX(BLUETOOTH): BLUETOOTH.4, TEENSY.7 (7/PWM/RX3)
TX(CAM): OPEN-MV.15 (TXD/SCL), TEENSY.0 (0/RX1/MOSI1)
TXE: JP1.5, U$4.6
TXN: JP1.7, U$4.4
TXS: JP1.3, U$4.8
TXW: JP1.2, U$4.10
UU: TEENSY.34 (34/A15/RX5)
UU2: TEENSY.33 (33/A14/TX5)

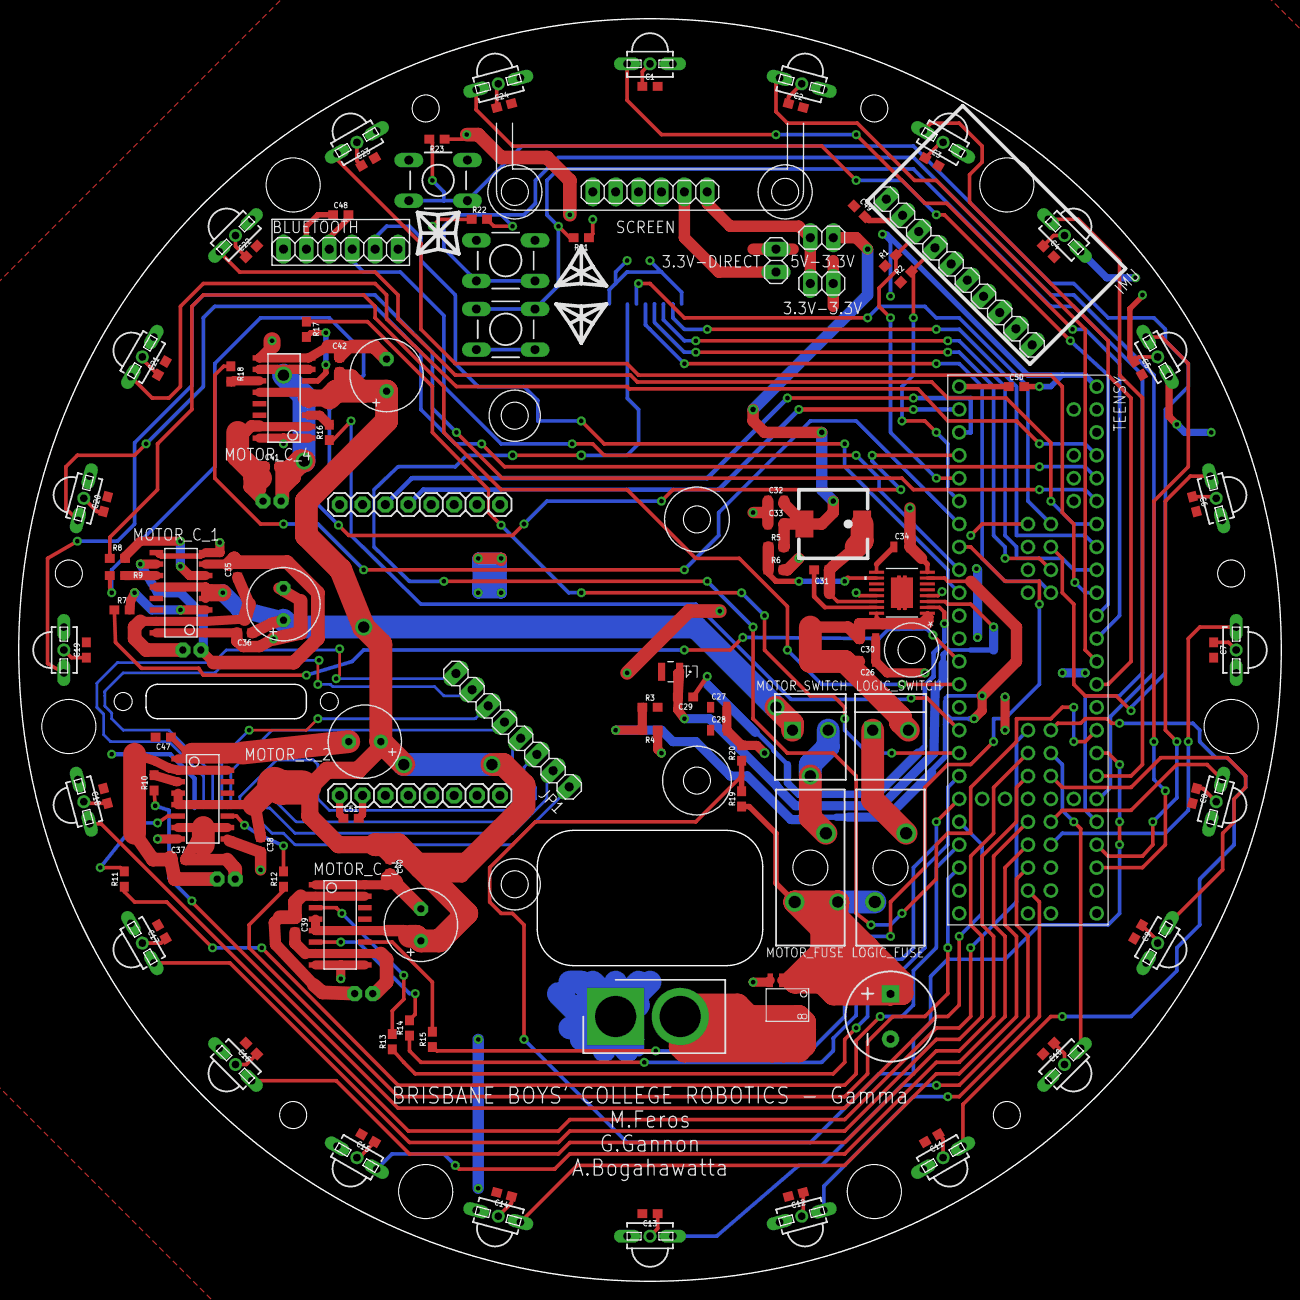
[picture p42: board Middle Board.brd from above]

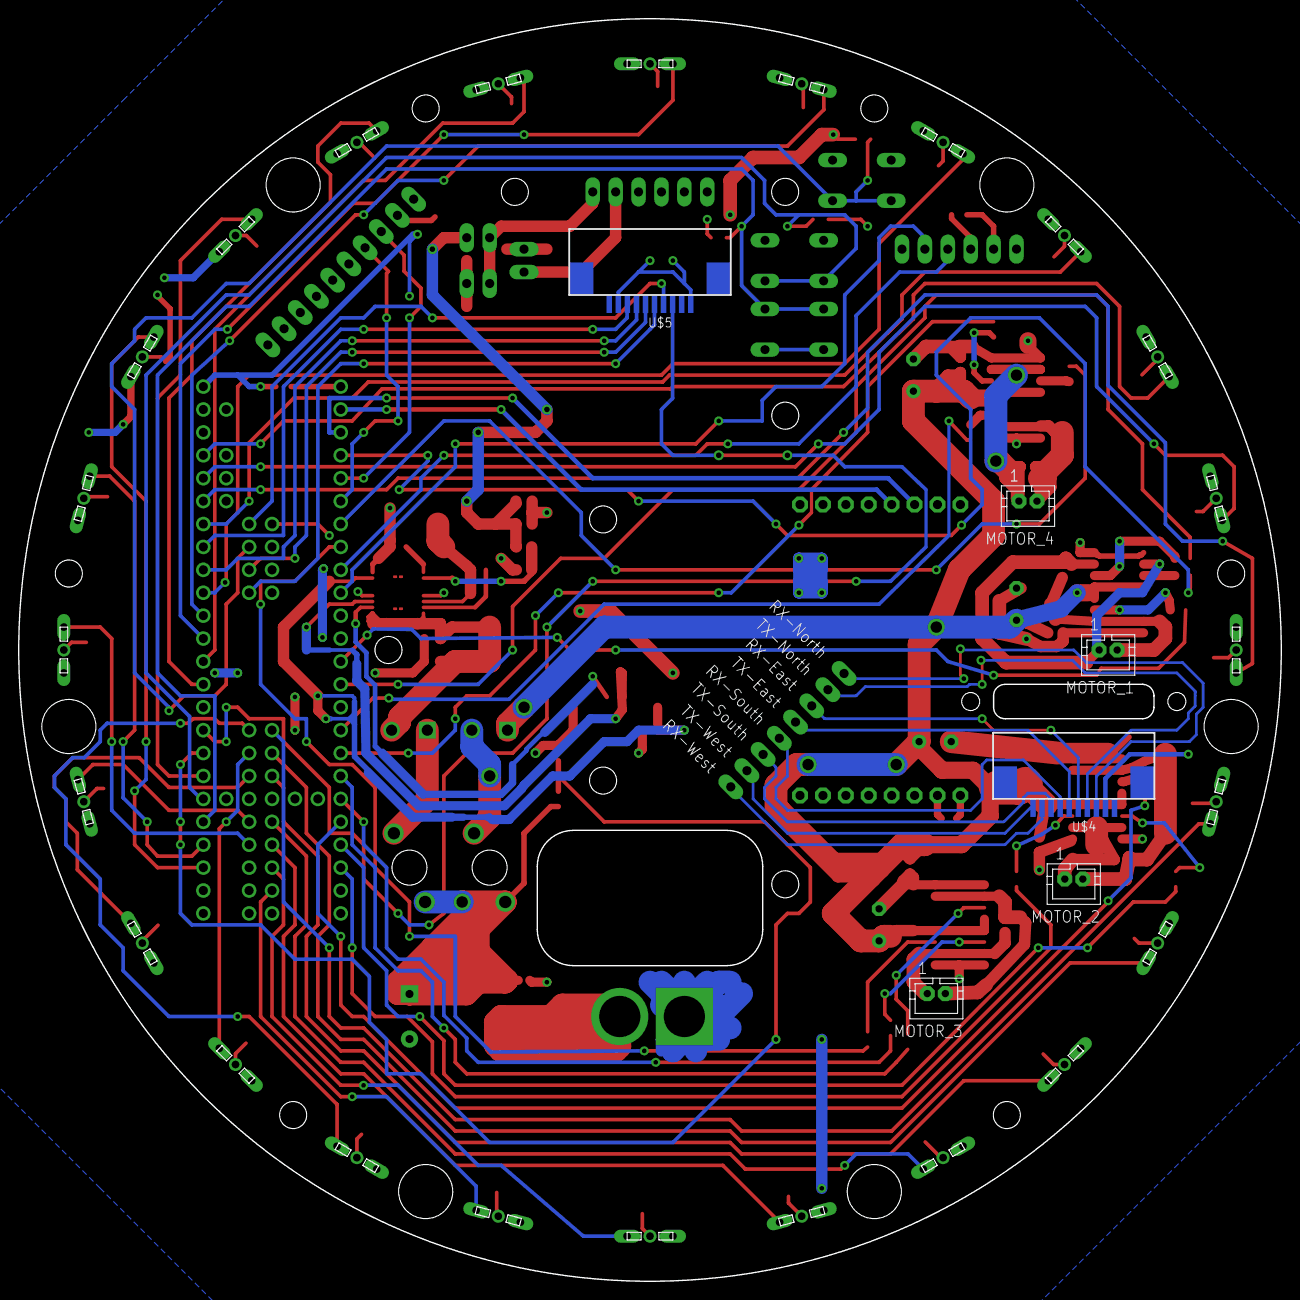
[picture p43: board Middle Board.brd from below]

Board: 2 copper layers, 140.0 x 140.0 mm, 129 parts (6 on the bottom side), 98 nets.

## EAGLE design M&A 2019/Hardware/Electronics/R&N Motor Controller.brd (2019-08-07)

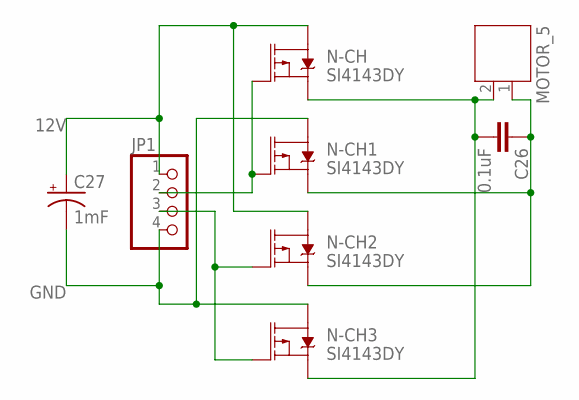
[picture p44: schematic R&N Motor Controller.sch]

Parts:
C26: 0.1uF; 0603
C27: 1mF; CPOL-RADIAL-5MM-10MM
JP1: PINHD-1X4; 1X04
MOTOR_5: JST-PH2
N-CH, N-CH1, N-CH2, N-CH3: SI4143DY; SO-8

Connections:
12V: C27.+, JP1.1, N-CH.5 (D), N-CH.6 (D), N-CH.7 (D), N-CH.8 (D), N-CH2.5 (D), N-CH2.6 (D), N-CH2.7 (D), N-CH2.8 (D)
GND: C27.-, JP1.4, N-CH1.5 (D), N-CH1.6 (D), N-CH1.7 (D), N-CH1.8 (D), N-CH3.5 (D), N-CH3.6 (D), N-CH3.7 (D), N-CH3.8 (D)
unnamed: C26.1, MOTOR_5.1, N-CH1.1 (S), N-CH1.2 (S), N-CH1.3 (S), N-CH2.1 (S), N-CH2.2 (S), N-CH2.3 (S)
unnamed: C26.2, MOTOR_5.2, N-CH.1 (S), N-CH.2 (S), N-CH.3 (S), N-CH3.1 (S), N-CH3.2 (S), N-CH3.3 (S)
PWM_INA: JP1.2, N-CH.4 (G), N-CH1.4 (G)
PWM_INB: JP1.3, N-CH2.4 (G), N-CH3.4 (G)

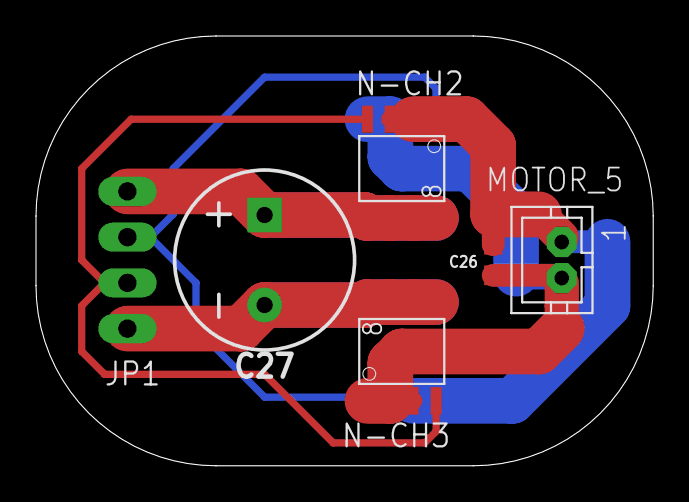
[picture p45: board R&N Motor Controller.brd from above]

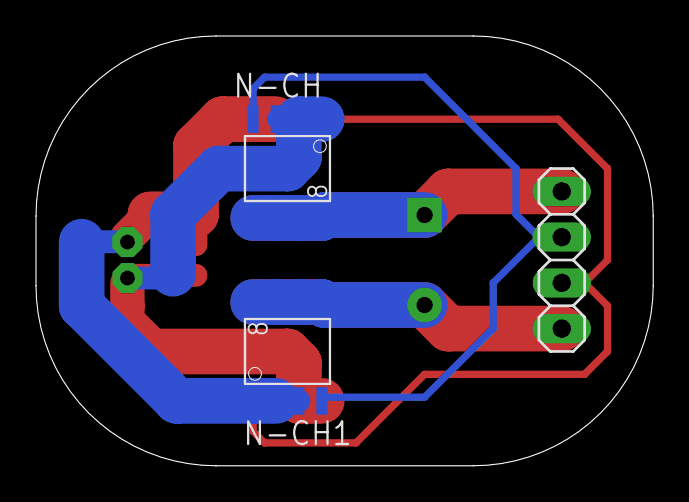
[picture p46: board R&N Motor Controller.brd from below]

Board: 2 copper layers, 34.3 x 23.9 mm, 8 parts (3 on the bottom side), 6 nets.

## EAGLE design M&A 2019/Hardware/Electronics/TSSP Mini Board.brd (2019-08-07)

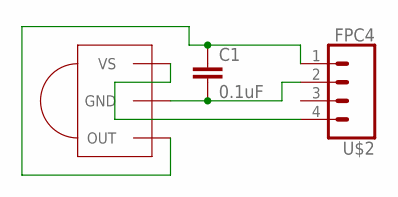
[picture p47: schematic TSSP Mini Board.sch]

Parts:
C1: 0.1uF; 0603
U$1: TSSP58038; MINICAST
U$2: FPC4

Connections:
unnamed: C1.1, U$1.1 (OUT), U$2.1
unnamed: C1.2, U$1.2 (GND), U$2.2
unnamed: U$1.3 (VS), U$2.4

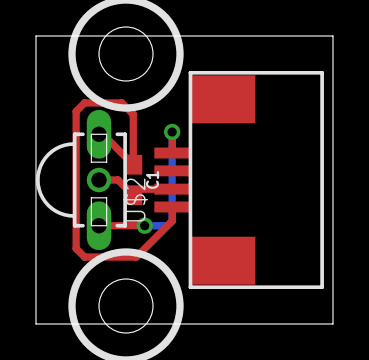
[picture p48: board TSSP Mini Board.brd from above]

Board: 2 copper layers, 16.5 x 16.0 mm, 3 parts (0 on the bottom side), 3 nets.

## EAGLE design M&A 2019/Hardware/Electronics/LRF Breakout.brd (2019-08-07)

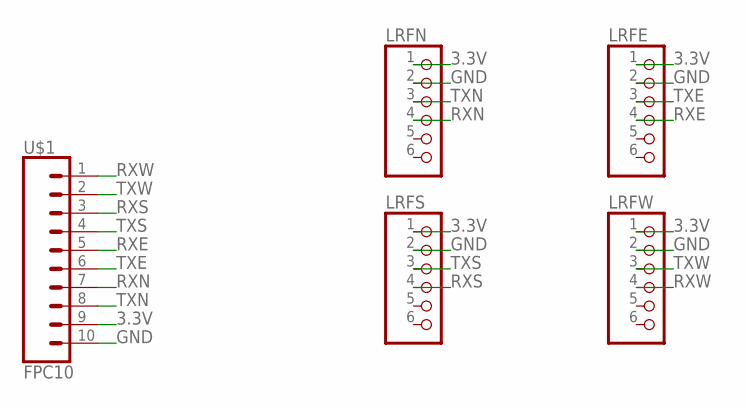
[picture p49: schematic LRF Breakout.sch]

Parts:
LRFE: PINHD-1X6; 1X06
LRFN: PINHD-1X6; 1X06
LRFS: PINHD-1X6; 1X06
LRFW: PINHD-1X6; 1X06
U$1: FPC10

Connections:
3.3V: LRFE.1, LRFN.1, LRFS.1, LRFW.1, U$1.9
GND: LRFE.2, LRFN.2, LRFS.2, LRFW.2, U$1.10
RXE: LRFE.4, U$1.5
RXN: LRFN.4, U$1.7
RXS: LRFS.4, U$1.3
RXW: LRFW.4, U$1.1
TXE: LRFE.3, U$1.6
TXN: LRFN.3, U$1.8
TXS: LRFS.3, U$1.4
TXW: LRFW.3, U$1.2

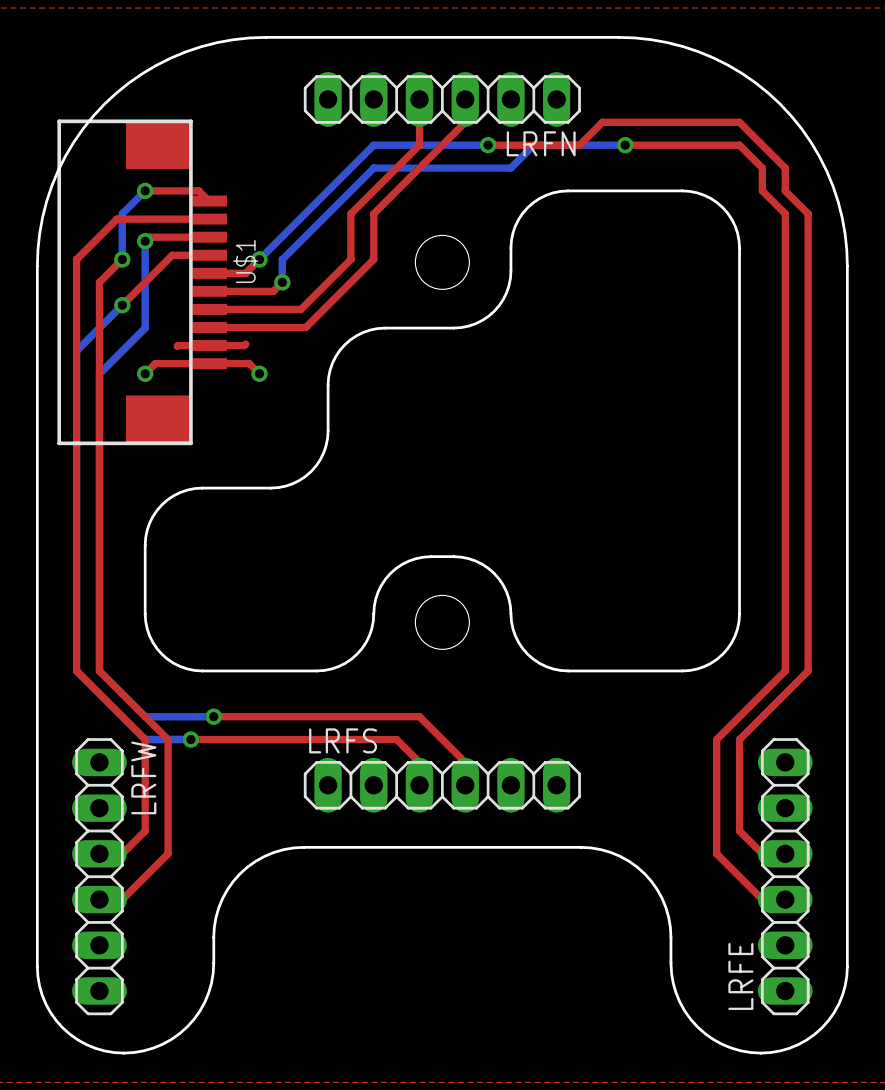
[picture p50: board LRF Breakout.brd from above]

Board: 2 copper layers, 45.0 x 56.4 mm, 5 parts (0 on the bottom side), 10 nets.

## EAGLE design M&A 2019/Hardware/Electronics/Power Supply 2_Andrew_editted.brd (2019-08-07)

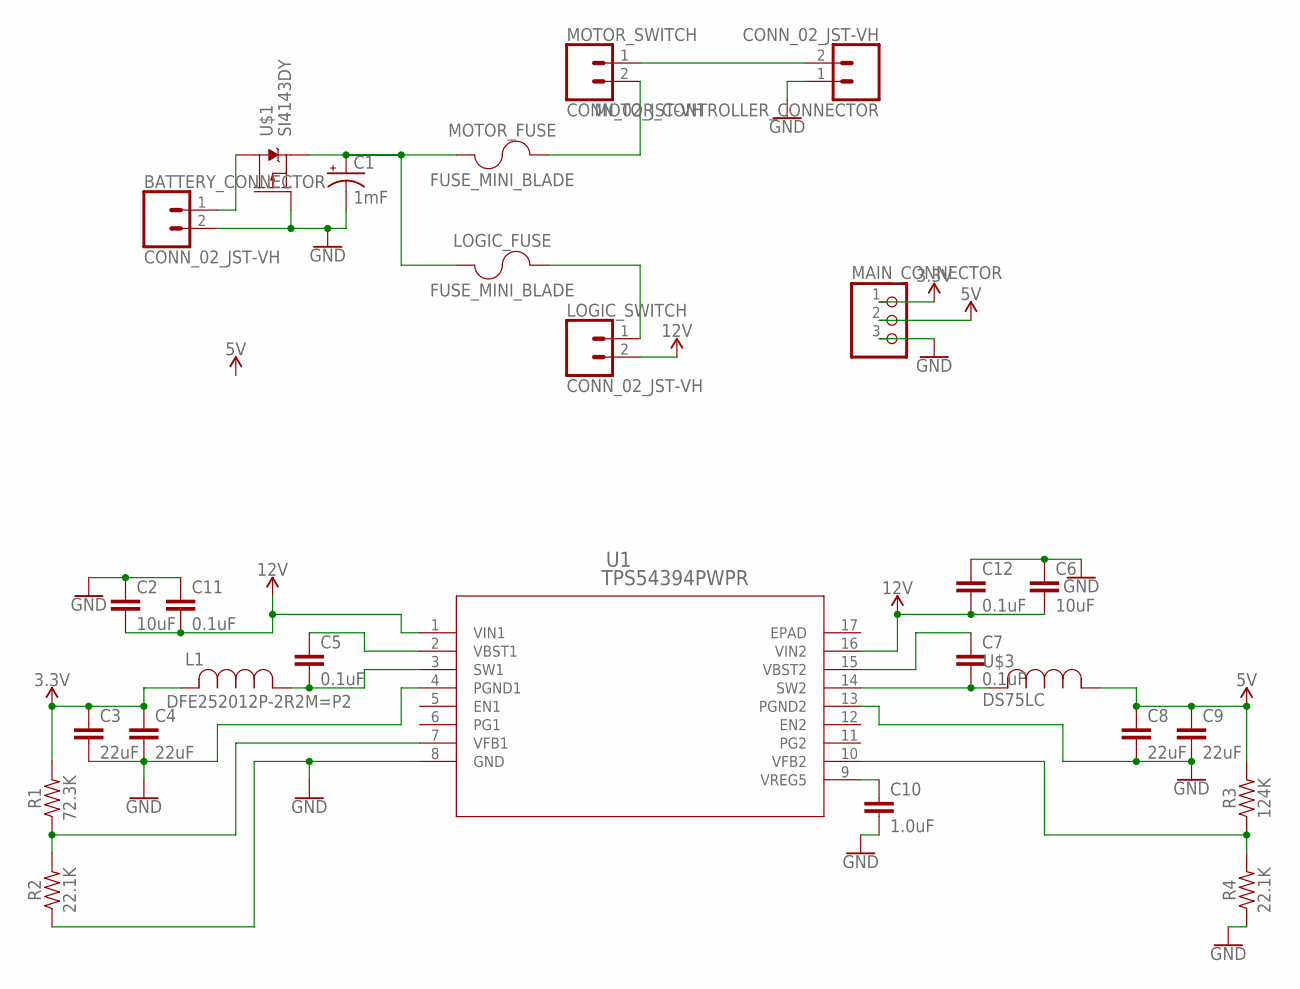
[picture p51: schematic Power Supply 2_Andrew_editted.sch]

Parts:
BATTERY_CONNECTOR: CONN_02_JST-VH; B2P-VH
C1: 1mF; CPOL-RADIAL-5MM-10MM
C2, C6: 10uF; 0805
C3, C4, C8, C9: 22uF; 0805
C5, C7, C11, C12: 0.1uF; 0603
C10: 1.0uF; 0805
L1: DFE252012P-2R2M=P2; DFE252012P-1R0M=P2
LOGIC_FUSE: FUSE_MINI_BLADE; SL-1538
LOGIC_SWITCH: CONN_02_JST-VH; B2P-VH
MAIN_CONNECTOR: PINHD-1X3; 1X03
MOTOR_CONTROLLER_CONNECTOR: CONN_02_JST-VH; B2P-VH
MOTOR_FUSE: FUSE_MINI_BLADE; SL-1538
MOTOR_SWITCH: CONN_02_JST-VH; B2P-VH
R1: 72.3K; 0603
R2, R4: 22.1K; 0603
R3: 124K; 0603
U1: TPS54394PWPR; PWP16_3P4X2P46
U$1: SI4143DY; SO-8
U$3: DS75LC

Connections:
3.3V: C3.1, C4.1, L1.2, MAIN_CONNECTOR.1, R1.2
5V: C8.1, C9.1, MAIN_CONNECTOR.2, R3.2, U$3.P$1 (1)
12V: C2.2, C6.2, C11.2, C12.2, LOGIC_SWITCH.2, U1.1 (VIN1), U1.16 (VIN2)
GND: BATTERY_CONNECTOR.2, C1.-, C2.1, C3.2, C4.2, C6.1, C8.2, C9.2, C10.2, C11.1, C12.1, MAIN_CONNECTOR.3, MOTOR_CONTROLLER_CONNECTOR.1, R2.1, R4.1, U1.4 (PGND1), U1.8 (GND), U1.13 (PGND2), U$1.4 (G)
unnamed: BATTERY_CONNECTOR.1, U$1.5 (D), U$1.6 (D), U$1.7 (D), U$1.8 (D)
unnamed: MOTOR_FUSE.P$2 (2), MOTOR_SWITCH.2
unnamed: C1.+, LOGIC_FUSE.P$1 (1), MOTOR_FUSE.P$1 (1), U$1.1 (S), U$1.2 (S), U$1.3 (S)
unnamed: LOGIC_FUSE.P$2 (2), LOGIC_SWITCH.1
unnamed: MOTOR_CONTROLLER_CONNECTOR.2, MOTOR_SWITCH.1
unnamed: C5.1, U1.2 (VBST1)
unnamed: C5.2, L1.1, U1.3 (SW1)
unnamed: C7.1, U1.15 (VBST2)
unnamed: R1.1, R2.2, U1.7 (VFB1)
unnamed: C7.2, U1.14 (SW2), U$3.P$2 (2)
unnamed: C10.1, U1.9 (VREG5)
unnamed: R3.1, R4.2, U1.10 (VFB2)

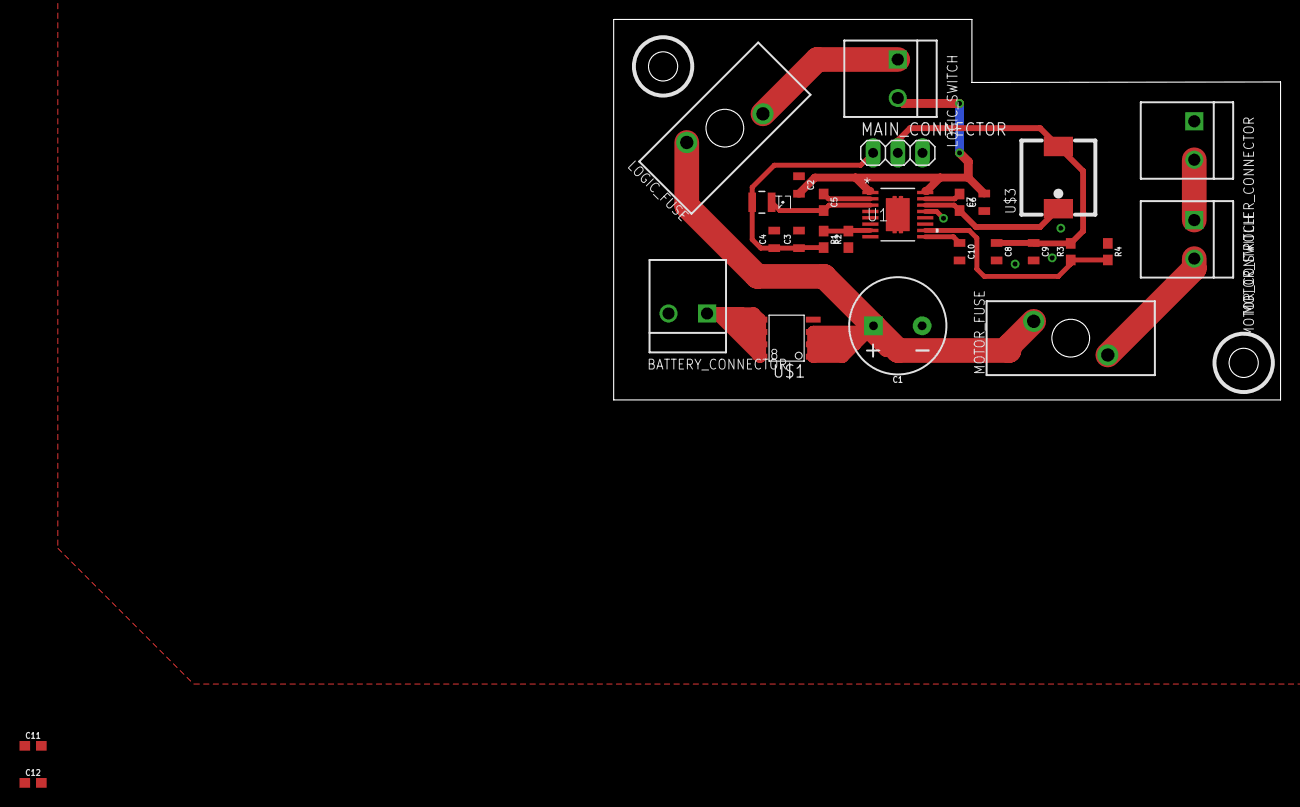
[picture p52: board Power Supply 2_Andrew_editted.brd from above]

Board: 2 copper layers, 68.6 x 39.1 mm, 27 parts (0 on the bottom side), 16 nets.

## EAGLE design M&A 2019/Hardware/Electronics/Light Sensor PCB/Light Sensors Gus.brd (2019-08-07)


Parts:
C1, C2, C3, C4, C5, C6, C7, C8, C9, C10, C11, C12, C13, C14, C15, C16, C17, C18, C19, C20, C21, C22, C23, C24, C25, C26, C27, C28, C29, C30, C31, C32: 0.1uF; C0603
LED0, LED1, LED2, LED3, LED4, LED5, LED6, LED7, LED8, LED9, LED10, LED11, LED12, LED13, LED14, LED15, LED16, LED17, LED18, LED19, LED20, LED21, LED22, LED23, LED24, LED25, LED26, LED27, LED28, LED29, LED30, LED31: LEDCHIPLED_0603; CHIPLED_0603
LS0, LS1, LS2, LS3, LS4, LS5, LS6, LS7, LS8, LS9, LS10, LS11, LS12, LS13, LS14, LS15, LS16, LS17, LS18, LS19, LS20, LS21, LS22, LS23, LS24, LS25, LS26, LS27, LS28, LS29, LS30, LS31: ALS; SMD
R1, R3, R5, R7, R9, R11, R13, R15, R17, R19, R21, R23, R25, R27, R29, R31, R33, R35, R37, R39, R41, R43, R45, R47, R49, R51, R53, R55, R57, R59, R61, R63: 100; R0603
R2, R4, R6, R8, R10, R12, R14, R16, R18, R20, R22, R24, R26, R28, R30, R32, R34, R36, R38, R40, R42, R44, R46, R48, R50, R52, R54, R56, R58, R60, R62, R64: 33K; R0603
U1: ADG732BSUZ-REEL; SU_48
U$2: FPC10

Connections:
+3V3: LS0.C, LS1.C, LS2.C, LS3.C, LS4.C, LS5.C, LS6.C, LS7.C, LS8.C, LS9.C, LS10.C, LS11.C, LS12.C, LS13.C, LS14.C, LS15.C, LS16.C, LS17.C, LS18.C, LS19.C, LS20.C, LS21.C, LS22.C, LS23.C, LS24.C, LS25.C, LS26.C, LS27.C, LS28.C, LS29.C, LS30.C, LS31.C, R1.2, R3.2, R5.2, R7.2, R9.2, R11.2, R13.2, R15.2, R17.2, R19.2, R21.2, R23.2, R25.2, R27.2, R29.2, R31.2, R33.2, R35.2, R37.2, R39.2, R41.2, R43.2, R45.2, R47.2, R49.2, R51.2, R53.2, R55.2, R57.2, R59.2, R61.2, R63.2, U1.13 (VDD_2), U1.14 (VDD), U$2.2, U$2.10
CONTROL1: U1.19 (A4), U$2.3
CONTROL2: U1.18 (A3), U$2.4
CONTROL3: U1.17 (A2), U$2.5
CONTROL4: U1.16 (A1), U$2.6
CONTROL5: U1.15 (A0), U$2.7
GND: C1.1, C2.1, C3.1, C4.1, C5.1, C6.1, C7.1, C8.1, C9.1, C10.1, C11.1, C12.1, C13.1, C14.1, C15.1, C16.1, C17.1, C18.1, C19.1, C20.1, C21.1, C22.1, C23.1, C24.1, C25.1, C26.1, C27.1, C28.1, C29.1, C30.1, C31.1, C32.1, LED0.C, LED1.C, LED2.C, LED3.C, LED4.C, LED5.C, LED6.C, LED7.C, LED8.C, LED9.C, LED10.C, LED11.C, LED12.C, LED13.C, LED14.C, LED15.C, LED16.C, LED17.C, LED18.C, LED19.C, LED20.C, LED21.C, LED22.C, LED23.C, LED24.C, LED25.C, LED26.C, LED27.C, LED28.C, LED29.C, LED30.C, LED31.C, R2.1, R4.1, R6.1, R8.1, R10.1, R12.1, R14.1, R16.1, R18.1, R20.1, R22.1, R24.1, R26.1, R28.1, R30.1, R32.1, R34.1, R36.1, R38.1, R40.1, R42.1, R44.1, R46.1, R48.1, R50.1, R52.1, R54.1, R56.1, R58.1, R60.1, R62.1, R64.1, U1.20 (!_2), U1.21 (!_3), U1.22 (!), U1.23 (GND), U1.24 (VSS), U$2.1, U$2.9
LS0: C1.2, LS0.E, R2.2, U1.36 (S28)
LS1: C2.2, LS1.E, R4.2, U1.35 (S27)
LS2: C3.2, LS2.E, R6.2, U1.34 (S26)
LS3: C4.2, LS3.E, R8.2, U1.33 (S25)
LS4: C5.2, LS4.E, R10.2, U1.32 (S24)
LS5: C6.2, LS5.E, R12.2, U1.31 (S23)
LS6: C7.2, LS6.E, R14.2, U1.30 (S22)
LS7: C8.2, LS7.E, R16.2, U1.29 (S21)
LS8: C9.2, LS8.E, R18.2, U1.28 (S20)
LS9: C10.2, LS9.E, R20.2, U1.27 (S19)
LS10: C11.2, LS10.E, R22.2, U1.26 (S18)
LS11: C12.2, LS11.E, R24.2, U1.25 (S17)
LS12: C13.2, LS12.E, R26.2, U1.12 (S1)
LS13: C14.2, LS13.E, R28.2, U1.11 (S2)
LS14: C15.2, LS14.E, R30.2, U1.10 (S3)
LS15: C16.2, LS15.E, R32.2, U1.9 (S4)
LS16: C17.2, LS16.E, R34.2, U1.8 (S5)
LS17: C18.2, LS17.E, R36.2, U1.7 (S6)
LS18: C19.2, LS18.E, R38.2, U1.6 (S7)
LS19: C20.2, LS19.E, R40.2, U1.5 (S8)
LS20: C21.2, LS20.E, R42.2, U1.4 (S9)
LS21: C22.2, LS21.E, R44.2, U1.3 (S10)
LS22: C23.2, LS22.E, R46.2, U1.2 (S11)
LS23: C24.2, LS23.E, R48.2, U1.1 (S12)
LS24: C25.2, LS24.E, R50.2, U1.48 (S13)
LS25: C26.2, LS25.E, R52.2, U1.47 (S14)
LS26: C27.2, LS26.E, R54.2, U1.46 (S15)
LS27: C28.2, LS27.E, R56.2, U1.45 (S16)
LS28: C29.2, LS28.E, R58.2, U1.40 (S32)
LS29: C30.2, LS29.E, R60.2, U1.39 (S31)
LS30: C31.2, LS30.E, R62.2, U1.38 (S30)
LS31: C32.2, LS31.E, R64.2, U1.37 (S29)
unnamed: LED0.A, R1.1
unnamed: LED1.A, R3.1
unnamed: LED2.A, R5.1
unnamed: LED3.A, R7.1
unnamed: LED4.A, R9.1
unnamed: LED5.A, R11.1
unnamed: LED6.A, R13.1
unnamed: LED7.A, R15.1
unnamed: LED8.A, R17.1
unnamed: LED9.A, R19.1
unnamed: LED10.A, R21.1
unnamed: LED11.A, R23.1
unnamed: LED12.A, R25.1
unnamed: LED13.A, R27.1
unnamed: LED14.A, R29.1
unnamed: LED15.A, R31.1
unnamed: LED16.A, R33.1
unnamed: LED17.A, R35.1
unnamed: LED18.A, R37.1
unnamed: LED19.A, R39.1
unnamed: LED20.A, R41.1
unnamed: LED21.A, R43.1
unnamed: LED22.A, R45.1
unnamed: LED23.A, R47.1
unnamed: LED24.A, R49.1
unnamed: LED25.A, R51.1
unnamed: LED26.A, R53.1
unnamed: LED27.A, R55.1
unnamed: LED28.A, R57.1
unnamed: LED29.A, R59.1
unnamed: LED30.A, R61.1
unnamed: LED31.A, R63.1
OUTPUT: U1.43 (D), U$2.8



Board: 2 copper layers, 120.0 x 120.0 mm, 162 parts (64 on the bottom side), 72 nets.

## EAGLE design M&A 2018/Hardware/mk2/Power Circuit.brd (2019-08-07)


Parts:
C1: 1mF; CPOL-RADIAL-5MM-10MM
C2: 0.33uF; C5B3
C3: 0.1uF; C5B3
D1: SCHOTTKY-DIODEP6T15; P6T15
JP1: PINHD-2X6; 2X06
U$1: BATT; B2P-VH
U$2: MOTOR FUSE; SL-1538
U$3: MOTOR SWITCH; B2P-VH
U$4, U$5: CONN_03_JST-VH; B3P-VH
U$6: LOGIC FUSE; SL-1538
U$7: LOGIC SWITCH; B2P-VH
U$8: LM7805; TO220-ADJ

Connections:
GND: C1.-, C2.2, C3.2, JP1.1, JP1.3, JP1.5, JP1.7, JP1.9, JP1.11, U$1.2, U$4.2, U$5.2, U$8.GND
unnamed: D1.A, U$1.1
unnamed: C1.+, D1.C, U$2.P$1 (1), U$6.P$1 (1)
unnamed: U$3.1, U$4.1, U$5.1
unnamed: U$2.P$2 (2), U$3.2
unnamed: U$6.P$2 (2), U$7.2
unnamed: C2.1, U$7.1, U$8.INPUT (IN)
unnamed: C3.1, JP1.2, JP1.4, JP1.6, JP1.8, JP1.10, JP1.12, U$4.3, U$5.3, U$8.OUTPUT (OUT)


Board: 2 copper layers, 94.9 x 39.8 mm, 12 parts (0 on the bottom side), 8 nets.

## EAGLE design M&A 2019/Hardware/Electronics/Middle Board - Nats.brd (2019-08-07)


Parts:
3.3V-3.3V, 3.3V-DIRECT, 5V-3.3V: PINHD-1X2; 1X02
BLUETOOTH: PINHD-1X6; 1X06
C1, C2, C3, C4, C5, C6, C7, C8, C9, C10, C11, C12, C13, C14, C15, C16, C17, C18, C19, C20, C21, C22, C23, C24, C34, C48, C49, C50, C51: 0.1uF; 0603
C25: 1mF; CPOL-RADIAL-5MM-10MM
C26, C28, C30, C32: 0.1UF_CAPACITOR_SMD; SPARKFUN-CAPACITORS_0603-CAP
C27, C29, C31, C33: 470uF; E3,5-8
C52, C54, C55: 10uF; SPARKFUN-CAPACITORS_0805
C53: 22uF; SPARKFUN-CAPACITORS_1206
CN1: B2P-VH
D2: ADAFRUIT_DIODE_SOD-123FL:1; ADAFRUIT_SOD-123FL
DOWN: DTS-6
IMU: PINHD-1X4; 1X04
J1: PRT-10474; SHDR2W320P716_1X2_1574X813X158
LOGIC_FUSE: FUSE_MINI_BLADE; SL-1538
MOTOR_1, MOTOR_2, MOTOR_3, MOTOR_5: VNH5050ATR-E; SOP50P1030X247-36N
MOTOR_FUSE: FUSE_MINI_BLADE; SL-1538
OPEN-MV: OPENMV3
P1, P2, P3, P4: JST-PH2
P5: JST-PH4
R1, R2, R21, R22, R23: 10k; 0603
R5, R6, R7, R8, R9, R10, R12, R13, R14, R15, R17, R18, R24, R25, R27, R28: 1k; 0603
R11, R16, R26, R29: 4.7k; 0603
R19: 35.7kOhm; 0603
R20: 10.2kOhm; 0603
SCREEN: PINHD-1X6; 1X06
SELECT: DTS-6
TEENSY, TEENSY1: TEENSY-3.5
TSSP1, TSSP2, TSSP3, TSSP4, TSSP5, TSSP6, TSSP7, TSSP8, TSSP9, TSSP10, TSSP11, TSSP12, TSSP13, TSSP14, TSSP15, TSSP16, TSSP17, TSSP18, TSSP19, TSSP20, TSSP21, TSSP22, TSSP23, TSSP24: TSSP58038; MINICAST
U$1, U$3: MINI_SWITCH; SWITCH
U$2: SI4143DY; SO-8
U$5: FPC10
UP: DTS-6
VREG-3.3: LINEAR_LM340S-05; LINEAR_TO263-3
VREG-5: V78-2000-SWITCHING-REGULATOR_V78-2000

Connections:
3.3V: 3.3V-3.3V.1, 3.3V-DIRECT.1, BLUETOOTH.2, C1.2, C2.2, C3.2, C4.2, C5.2, C6.2, C7.2, C8.2, C9.2, C10.2, C11.2, C12.2, C13.2, C14.2, C15.2, C16.2, C17.2, C18.2, C19.2, C20.2, C21.2, C22.2, C23.2, C24.2, C34.1, C48.1, C49.1, C50.1, C51.2, C55.1, DOWN.1, DOWN.2, IMU.1, OPEN-MV.27 (VIN), R1.1, R2.1, SELECT.1, SELECT.2, TEENSY.3.3V, TEENSY.3.3V-1, TEENSY.3.3V-2, TEENSY.3.3V-3, TEENSY1.3.3V-1, TEENSY1.3.3V-2, TEENSY1.3.3V-3, TSSP1.1 (OUT), TSSP2.1 (OUT), TSSP3.1 (OUT), TSSP4.1 (OUT), TSSP5.1 (OUT), TSSP6.1 (OUT), TSSP7.1 (OUT), TSSP8.1 (OUT), TSSP9.1 (OUT), TSSP10.1 (OUT), TSSP11.1 (OUT), TSSP12.1 (OUT), TSSP13.1 (OUT), TSSP14.1 (OUT), TSSP15.1 (OUT), TSSP16.1 (OUT), TSSP17.1 (OUT), TSSP18.1 (OUT), TSSP19.1 (OUT), TSSP20.1 (OUT), TSSP21.1 (OUT), TSSP22.1 (OUT), TSSP23.1 (OUT), TSSP24.1 (OUT), U$5.1, U$5.9, UP.1, UP.2, VREG-3.3.2 (VO), VREG-3.3.TAB (VO)
5V: 5V-3.3V.1, C53.1, D2.A, R11.2, R16.2, R26.2, R29.2, VREG-5.3 (VOUT)
12V: C27.+, C29.+, C31.+, C33.+, CN1.1, MOTOR_1.13 (VCC-1), MOTOR_1.24 (VCC-2), MOTOR_1.SLUG1 (VCC-1), MOTOR_2.13 (VCC-1), MOTOR_2.24 (VCC-2), MOTOR_2.SLUG1 (VCC-1), MOTOR_3.13 (VCC-1), MOTOR_3.24 (VCC-2), MOTOR_3.SLUG1 (VCC-1), MOTOR_5.13 (VCC-1), MOTOR_5.24 (VCC-2), MOTOR_5.SLUG1 (VCC-1), P5.1, U$3.P$1 (O)
BATTERY-VOLTAGE(ANALOG): R19.2, R20.1
BDOWN: DOWN.3, DOWN.4, R22.2
BSELECT: R23.2, SELECT.3, SELECT.4
BUP: R21.2, UP.3, UP.4
COMS-CS: TEENSY.31 (31/A12/RX4/CS1), TEENSY1.31 (31/A12/RX4/CS1)
COMS-MISO: TEENSY.1 (1/TX1/MISO1), TEENSY1.1 (1/TX1/MISO1)
COMS-MOSI: TEENSY.0 (0/RX1/MOSI1), TEENSY1.0 (0/RX1/MOSI1)
COMS-SCK: TEENSY.32 (32/A13/TX4/SCK1), TEENSY1.32 (32/A13/TX4/SCK1)
GND: BLUETOOTH.3, C1.1, C2.1, C3.1, C4.1, C5.1, C6.1, C7.1, C8.1, C9.1, C10.1, C11.1, C12.1, C13.1, C14.1, C15.1, C16.1, C17.1, C18.1, C19.1, C20.1, C21.1, C22.1, C23.1, C24.1, C25.-, C27.-, C29.-, C31.-, C33.-, C34.2, C48.2, C49.2, C50.2, C51.1, C52.2, C53.2, C54.2, C55.2, CN1.2, IMU.2, J1.1 (GND), MOTOR_1.1 (GND_A-1), MOTOR_1.3 (GND_A-2), MOTOR_1.4 (GND_A-3), MOTOR_1.5 (GND_A-4), MOTOR_1.6 (GND_A-5), MOTOR_1.7 (GND_A-6), MOTOR_1.30 (GND_B-1), MOTOR_1.31 (GND_B-2), MOTOR_1.32 (GND_B-3), MOTOR_1.33 (GND_B-4), MOTOR_1.34 (GND_B-5), MOTOR_1.36 (GND_B-6), MOTOR_2.1 (GND_A-1), MOTOR_2.3 (GND_A-2), MOTOR_2.4 (GND_A-3), MOTOR_2.5 (GND_A-4), MOTOR_2.6 (GND_A-5), MOTOR_2.7 (GND_A-6), MOTOR_2.30 (GND_B-1), MOTOR_2.31 (GND_B-2), MOTOR_2.32 (GND_B-3), MOTOR_2.33 (GND_B-4), MOTOR_2.34 (GND_B-5), MOTOR_2.36 (GND_B-6), MOTOR_3.1 (GND_A-1), MOTOR_3.3 (GND_A-2), MOTOR_3.4 (GND_A-3), MOTOR_3.5 (GND_A-4), MOTOR_3.6 (GND_A-5), MOTOR_3.7 (GND_A-6), MOTOR_3.30 (GND_B-1), MOTOR_3.31 (GND_B-2), MOTOR_3.32 (GND_B-3), MOTOR_3.33 (GND_B-4), MOTOR_3.34 (GND_B-5), MOTOR_3.36 (GND_B-6), MOTOR_5.1 (GND_A-1), MOTOR_5.3 (GND_A-2), MOTOR_5.4 (GND_A-3), MOTOR_5.5 (GND_A-4), MOTOR_5.6 (GND_A-5), MOTOR_5.7 (GND_A-6), MOTOR_5.30 (GND_B-1), MOTOR_5.31 (GND_B-2), MOTOR_5.32 (GND_B-3), MOTOR_5.33 (GND_B-4), MOTOR_5.34 (GND_B-5), MOTOR_5.36 (GND_B-6), OPEN-MV.28 (GND), P5.2, P5.4, R10.1, R15.1, R20.2, R21.1, R22.1, R23.1, R25.1, R28.1, SCREEN.4, TEENSY.GND, TEENSY.GND-1, TEENSY.GND-2, TEENSY.GND-3, TEENSY.GND-4, TEENSY1.GND, TEENSY1.GND-1, TEENSY1.GND-2, TEENSY1.GND-3, TEENSY1.GND-4, TSSP1.2 (GND), TSSP2.2 (GND), TSSP3.2 (GND), TSSP4.2 (GND), TSSP5.2 (GND), TSSP6.2 (GND), TSSP7.2 (GND), TSSP8.2 (GND), TSSP9.2 (GND), TSSP10.2 (GND), TSSP11.2 (GND), TSSP12.2 (GND), TSSP13.2 (GND), TSSP14.2 (GND), TSSP15.2 (GND), TSSP16.2 (GND), TSSP17.2 (GND), TSSP18.2 (GND), TSSP19.2 (GND), TSSP20.2 (GND), TSSP21.2 (GND), TSSP22.2 (GND), TSSP23.2 (GND), TSSP24.2 (GND), U$2.4 (G), U$5.2, U$5.10, VREG-3.3.1 (GND), VREG-5.2 (GND)
KICKER-SIG: P5.3
LS-CONTROL1: U$5.8
LS-CONTROL2: U$5.7
LS-CONTROL3: U$5.6
LS-CONTROL4: U$5.5
LS-CONTROL5: U$5.4
LS-OUTPUT: U$5.3
MOTOR-BL(ENA): R17.1
MOTOR-BL(ENB): R18.1
MOTOR-BL(PWM): R27.1, R28.2
MOTOR-BR(ENA): R12.1
MOTOR-BR(ENB): R13.1
MOTOR-BR(PWM): R14.1, R15.2
MOTOR-FL(ENA): R7.1
MOTOR-FL(ENB): R8.1
MOTOR-FL(PWM): R9.1, R10.2
MOTOR-FR(ENA): R5.1
MOTOR-FR(ENB): R6.1
MOTOR-FR(PWM): R24.1, R25.2
unnamed: J1.2 (POS), U$2.5 (D), U$2.6 (D), U$2.7 (D), U$2.8 (D)
unnamed: MOTOR_FUSE.P$2 (2), U$3.P$2
unnamed: C25.+, LOGIC_FUSE.P$1 (1), MOTOR_FUSE.P$1 (1), R19.1, U$2.1 (S), U$2.2 (S), U$2.3 (S)
unnamed: LOGIC_FUSE.P$2 (2), U$1.P$1 (O)
unnamed: MOTOR_1.15 (INA), R7.2
unnamed: MOTOR_5.15 (INA), R5.2
unnamed: MOTOR_5.17 (PWM), R24.2
unnamed: MOTOR_5.22 (INB), R6.2
unnamed: C26.1, MOTOR_5.2 (OUT.A-1), MOTOR_5.8 (OUT.A-2), MOTOR_5.9 (OUT.A-3), MOTOR_5.10 (OUT.A-4), MOTOR_5.11 (OUT.A-5), MOTOR_5.12 (OUT.A-6), MOTOR_5.14 (OUT.A-7), MOTOR_5.SLUG2 (OUT.A-1), P1.2
unnamed: MOTOR_1.22 (INB), R8.2
unnamed: MOTOR_5.19 (CS), MOTOR_5.20 (CS_DIS)
unnamed: C26.2, MOTOR_5.23 (OUT.B-1), MOTOR_5.25 (OUT.B-2), MOTOR_5.26 (OUT.B-3), MOTOR_5.27 (OUT.B-4), MOTOR_5.28 (OUT.B-5), MOTOR_5.29 (OUT.B-6), MOTOR_5.35 (OUT.B-7), MOTOR_5.SLUG3 (OUT.B-1), P1.1
unnamed: MOTOR_1.17 (PWM), R9.2
unnamed: MOTOR_1.19 (CS), MOTOR_1.20 (CS_DIS)
unnamed: C28.2, MOTOR_1.23 (OUT.B-1), MOTOR_1.25 (OUT.B-2), MOTOR_1.26 (OUT.B-3), MOTOR_1.27 (OUT.B-4), MOTOR_1.28 (OUT.B-5), MOTOR_1.29 (OUT.B-6), MOTOR_1.35 (OUT.B-7), MOTOR_1.SLUG3 (OUT.B-1), P2.1
unnamed: C28.1, MOTOR_1.2 (OUT.A-1), MOTOR_1.8 (OUT.A-2), MOTOR_1.9 (OUT.A-3), MOTOR_1.10 (OUT.A-4), MOTOR_1.11 (OUT.A-5), MOTOR_1.12 (OUT.A-6), MOTOR_1.14 (OUT.A-7), MOTOR_1.SLUG2 (OUT.A-1), P2.2
unnamed: MOTOR_1.16 (EN-A), MOTOR_1.21 (EN-B), R11.1
unnamed: MOTOR_2.15 (INA), R12.2
unnamed: MOTOR_2.22 (INB), R13.2
unnamed: MOTOR_2.17 (PWM), R14.2
unnamed: MOTOR_2.19 (CS), MOTOR_2.20 (CS_DIS)
unnamed: C30.2, MOTOR_2.23 (OUT.B-1), MOTOR_2.25 (OUT.B-2), MOTOR_2.26 (OUT.B-3), MOTOR_2.27 (OUT.B-4), MOTOR_2.28 (OUT.B-5), MOTOR_2.29 (OUT.B-6), MOTOR_2.35 (OUT.B-7), MOTOR_2.SLUG3 (OUT.B-1), P3.1
unnamed: C30.1, MOTOR_2.2 (OUT.A-1), MOTOR_2.8 (OUT.A-2), MOTOR_2.9 (OUT.A-3), MOTOR_2.10 (OUT.A-4), MOTOR_2.11 (OUT.A-5), MOTOR_2.12 (OUT.A-6), MOTOR_2.14 (OUT.A-7), MOTOR_2.SLUG2 (OUT.A-1), P3.2
unnamed: MOTOR_2.16 (EN-A), MOTOR_2.21 (EN-B), R16.1
unnamed: MOTOR_3.15 (INA), R17.2
unnamed: MOTOR_3.22 (INB), R18.2
unnamed: MOTOR_3.17 (PWM), R27.2
unnamed: MOTOR_3.19 (CS), MOTOR_3.20 (CS_DIS)
unnamed: C32.2, MOTOR_3.23 (OUT.B-1), MOTOR_3.25 (OUT.B-2), MOTOR_3.26 (OUT.B-3), MOTOR_3.27 (OUT.B-4), MOTOR_3.28 (OUT.B-5), MOTOR_3.29 (OUT.B-6), MOTOR_3.35 (OUT.B-7), MOTOR_3.SLUG3 (OUT.B-1), P4.1
unnamed: C32.1, MOTOR_3.2 (OUT.A-1), MOTOR_3.8 (OUT.A-2), MOTOR_3.9 (OUT.A-3), MOTOR_3.10 (OUT.A-4), MOTOR_3.11 (OUT.A-5), MOTOR_3.12 (OUT.A-6), MOTOR_3.14 (OUT.A-7), MOTOR_3.SLUG2 (OUT.A-1), P4.2
unnamed: MOTOR_5.16 (EN-A), MOTOR_5.21 (EN-B), R26.1
unnamed: MOTOR_3.16 (EN-A), MOTOR_3.21 (EN-B), R29.1
unnamed: 3.3V-DIRECT.2, SCREEN.5
unnamed: 3.3V-3.3V.2, 5V-3.3V.2, SCREEN.6
unnamed: C52.1, U$1.P$2, VREG-5.1 (VIN)
unnamed: C54.1, D2.C, VREG-3.3.3 (VI)
RX(BLUETOOTH): BLUETOOTH.5, TEENSY.10 (10/PWM/TX2/CS0)
RX(CAM): OPEN-MV.16 (RXD/SDA)
SCL(IMU): IMU.3, R1.2, TEENSY.3 (3/PWM/CAN0TX/SCL2)
SCREEN(SCL): SCREEN.2
SCREEN(SDA): SCREEN.1
SDA(IMU): IMU.4, R2.2, TEENSY.4 (4/PWM/CAN0RX/SDA2)
TSSP1: TSSP1.3 (VS)
TSSP2: TSSP2.3 (VS)
TSSP3: TSSP3.3 (VS)
TSSP4: TSSP4.3 (VS)
TSSP5: TSSP5.3 (VS)
TSSP6: TSSP6.3 (VS)
TSSP7: TSSP7.3 (VS)
TSSP8: TSSP8.3 (VS)
TSSP9: TSSP9.3 (VS)
TSSP10: TSSP10.3 (VS)
TSSP11: TSSP11.3 (VS)
TSSP12: TSSP12.3 (VS)
TSSP13: TSSP13.3 (VS)
TSSP14: TSSP14.3 (VS)
TSSP15: TSSP15.3 (VS)
TSSP16: TSSP16.3 (VS)
TSSP17: TSSP17.3 (VS)
TSSP18: TSSP18.3 (VS)
TSSP19: TSSP19.3 (VS)
TSSP20: TSSP20.3 (VS)
TSSP21: TSSP21.3 (VS)
TSSP22: TSSP22.3 (VS)
TSSP23: TSSP23.3 (VS)
TSSP24: TSSP24.3 (VS)
TX(BLUETOOTH): BLUETOOTH.4, TEENSY.9 (9/PWM/RX2/CS0)
TX(CAM): OPEN-MV.15 (TXD/SCL)



Board: 2 copper layers, 140.0 x 140.0 mm, 125 parts (14 on the bottom side), 56 nets.

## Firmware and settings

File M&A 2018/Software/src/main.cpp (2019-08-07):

#include <PixyI2C.h>
#include <tsops.h>
#include <LightSensors.h>
#include <IMU.h>
#include <Motors.h>
#include <PID.h>
#include <Arduino.h>
#include <I2C.h>
#include <SparkFun_VL53L1X_Arduino_Library.h>
#include <Timer.h>
// #include <Bluetooth.h>

PixyI2C pixy;
Tsops tsops;
LightSensors lights;
Motors motors;
IMU IMU;
PID headingPID(HEADING_KP, HEADING_KI, HEADING_KD, HEADING_MAX_CORRECTION);
PID goalTrackPID(CAMERA_KP, CAMERA_KI, CAMERA_KD, CAMERA_MAX_CORRECTION);
PID goalTrackWeakPID(CAMERA_WEAK_KP, CAMERA_WEAK_KI, CAMERA_WEAK_KD, CAMERA_WEAK_MAX_CORRECTION);
PID goalTrackDefendPID(CAMERA_DEFEND_KP, CAMERA_DEFEND_KI, CAMERA_DEFEND_KD, CAMERA_DEFEND_MAX_CORRECTION);
PID centreDistancePID(CENTRE_DISTANCE_KP, CENTRE_DISTANCE_KI, CENTRE_DISTANCE_KD);
PID defendSidewaysPID(DEFEND_SIDEWAYS_KP, DEFEND_SIDEWAYS_KI, DEFEND_SIDEWAYS_KD, DEFEND_SIDEWAYS_MAX_SPEED);
PID centreSidewaysPID(CENTRE_SIDEWAYS_KP, CENTRE_SIDEWAYS_KI, CENTRE_SIDEWAYS_KD);
Timer LEDTimer(((bool)DEFAULT_ROLE ? LED_BLINK_TIME_ATTACK : LED_BLINK_TIME_DEFEND));
Timer pixyTimer(PIXY_READ_RATE);
Timer switchTimer(BT_SWITCH_TIMER);
VL53L1X lrf;
// Bluetooth bluetooth(DEFAULT_ROLE);

DirSpeed finalMovement;
bool onField = true;
double fieldLineAngle = -1;
int fieldLineSize;
double goalAngle = 0;
bool goalVisible = false;
bool ledOn = false;
double lrfValue;
bool attacking = DEFAULT_ROLE;

void calculateOutAvoidance(DirSpeed move) {
    bool noLine = (lights.getLineDir() == -1);
    double lineDirection = noLine ? -1 : angleMap(lights.getLineDir() + IMU.getIMUHeading(), 360);
    if(onField) {
        if(!noLine) {
            fieldLineAngle = lineDirection;
            fieldLineSize = 1;
            onField = false;
        }
    } else {
        if(fieldLineSize == 3) {
            if(!noLine) {
                fieldLineAngle = angleMap(lineDirection + 180, 360);
                fieldLineSize = 2;
            }
        } else {
            if(noLine) {
                if(fieldLineSize == 1) {
                    onField = true;
                    fieldLineAngle = -1;
                    fieldLineSize = 0;
                } else {
                    fieldLineSize = 3;
                }
            } else {
                if(smallestAngleBetween(lineDirection, fieldLineAngle) <= 90) {
                    fieldLineAngle = lineDirection;
                    fieldLineSize = 1;
                } else {
                    fieldLineAngle = angleMap(lineDirection + 180, 360);
                    fieldLineSize = 2;
                }
            }
        }
    }
    if(!noLine) {
        finalMovement.direction = angleMap(fieldLineAngle + 180 - IMU.getIMUHeading(), 360);
        if(fieldLineSize == 1 && abs(finalMovement.direction - fieldLineAngle) < 60) {
            finalMovement.speed = 0;
        } else if(fieldLineSize == 2) {
            finalMovement.speed = abs(finalMovement.direction - fieldLineAngle) < 60 ? AVOID_SLOW_SPEED : AVOID_FAST_SPEED;
        }
    } else {
        if(fieldLineSize == 3) {
            finalMovement.direction = angleMap(fieldLineAngle + 180 - IMU.getIMUHeading(), 360);
            finalMovement.speed = abs(finalMovement.direction - fieldLineAngle) < 60 ? AVOID_SLOW_SPEED : AVOID_FAST_SPEED;
        }
    }
}

void calculateOrbit() {
    double ballAngleDifference = findSign(angleMap(tsops.getBallDir(), 180)) * fmin(90, 0.4 * pow(MATH_E, 0.15 * smallestAngleBetween(tsops.getBallDir(), 0)));
    double strengthFactor = constrain(tsops.getAvgStr() / BALL_CLOSE_STRENGTH, 0, 1);
    double distanceMultiplier = constrain((0.02 * strengthFactor * pow(MATH_E, 4.5 * strengthFactor)), 0, 1);
    double angleAddition = ballAngleDifference * distanceMultiplier;
    finalMovement.direction = angleMap(tsops.getBallDir() + angleAddition, 360);
    finalMovement.speed = ORBIT_SLOW_SPEED + (ORBIT_FAST_SPEED - ORBIT_SLOW_SPEED) * (1.0 - abs(angleAddition) / 90.0);
}

void calculateAttackingGoalAngle() {
    if(pixyTimer.timeHasPassed()) {
        int blocks = pixy.getBlocks();
        int goalIndex = -1;
        goalVisible = false;
        if(blocks != 0) {
            for(int i = 0; i < blocks; i++) {
                if(pixy.blocks[i].x > 160) {
                    goalVisible = true;
                    goalIndex = goalIndex == -1 ? i : goalIndex;
                }
            }
            goalAngle = ((PIXY_FRAME_HEIGHT / 2.0) - pixy.blocks[goalIndex].y) * MAX_ANGLING / (PIXY_FRAME_HEIGHT / 2.0);
        }
    }
    // goalVisible = false;
}

void calculateDefendingGoalAngle() {
    if(pixyTimer.timeHasPassed()) {
        int blocks = pixy.getBlocks();
        int goalIndex = -1;
        goalVisible = false;
        if(blocks != 0) {
            for(int i = 0; i < blocks; i++) {
                if(pixy.blocks[i].x < 160) {
                    goalVisible = true;
                    goalIndex = goalIndex == -1 ? i : goalIndex;
                }
            }
            goalAngle = -((PIXY_FRAME_HEIGHT / 2.0) - pixy.blocks[goalIndex].y) * MAX_ANGLING / (PIXY_FRAME_HEIGHT / 2.0);
        }
    }
    // goalVisible = false;
}

void calculateAttack() {
    calculateAttackingGoalAngle();
    double correction = IMU.getIMUHeading() > 180 ? angleMap((IMU.getIMUHeading() - 360), 180) : IMU.getIMUHeading();
    if(abs(angleMap(tsops.getBallDir() - 360, 180)) < 45) {
        correction = goalVisible ? -goalTrackPID.update(angleMap(correction + goalAngle, 180), 0) : -headingPID.update(angleMap(correction, 180), 0);
    } else {
        correction =  goalVisible ? -goalTrackWeakPID.update(angleMap(correction + goalAngle, 180), 0) : -headingPID.update(angleMap(correction, 180), 0);
    }
    calculateOrbit();
    calculateOutAvoidance(finalMovement);
    if(!tsops.getBallVisible()) {
        if(fieldLineAngle == -1) {
            finalMovement.speed = 0;
        }
    }
    motors.updateDirection(finalMovement.direction, correction, finalMovement.speed);
}

void calculateDefenseMovement() {
    double distanceMovement;
    double sidewaysMovement;
    bool surge = (lrfValue < 600);
    if(goalVisible) {
        if(tsops.getBallVisible()) {
            if(angleIsInside(270, 90, tsops.getBallDir())) {
                if(tsops.getAvgStr() > DEFEND_CHARGE_STRENGTH && angleIsInside(335, 25, tsops.getBallDir()) && surge) {
                    // attacking = true;
                    // LEDTimer.updateTimerDuration(LED_BLINK_TIME_ATTACK);
                    calculateOrbit();
                } else {
                    distanceMovement =  -centreDistancePID.update(lrfValue, DEFEND_GOAL_DISTANCE);
                    sidewaysMovement = abs(angleMap(tsops.getBallDir() - 360, 180)) > DEFEND_SMALL_ANGLE ? defendSidewaysPID.update(angleMap(tsops.getBallDir() - 360, 180), 0) : 0;
                    finalMovement.direction = angleMap(RADIANS_TO_DEGREES * atan2(sidewaysMovement, distanceMovement), 360);
                    finalMovement.speed = sqrt(distanceMovement * distanceMovement + sidewaysMovement * sidewaysMovement);
                }
            } else {
                calculateOrbit();
            }
        } else {
            distanceMovement =  -centreDistancePID.update(lrfValue, DEFEND_GOAL_DISTANCE);
            sidewaysMovement = centreSidewaysPID.update(angleMap(IMU.getIMUHeading() - 360, 180), 0);
            finalMovement.direction = angleMap(RADIANS_TO_DEGREES * atan2(sidewaysMovement, distanceMovement), 360);
            finalMovement.speed = distanceMovement;
        }
    } else if(tsops.getBallVisible()) {
        if(angleIsInside(270, 90, tsops.getBallDir())) {
            distanceMovement = angleIsInside(345, 15, IMU.getIMUHeading()) ? -centreDistancePID.update(lrfValue, DEFEND_BLOCK_DISTANCE) : 0;
            sidewaysMovement = defendSidewaysPID.update(angleMap(tsops.getBallDir() - 360, 180), 0);
            finalMovement.direction = angleMap(RADIANS_TO_DEGREES * atan2(sidewaysMovement, distanceMovement), 360);
            finalMovement.speed = sqrt(distanceMovement * distanceMovement + sidewaysMovement * sidewaysMovement);
        } else {
            calculateOrbit();
        }
    } else {
        distanceMovement = -centreDistancePID.update(lrfValue, DEFEND_BLOCK_DISTANCE);
        finalMovement.direction = angleMap(RADIANS_TO_DEGREES * atan2(0, distanceMovement), 360);
        finalMovement.speed = distanceMovement;
    }
}

void calculateDefense() {
    calculateDefendingGoalAngle();
    double correction = IMU.getIMUHeading() > 180 ? angleMap((IMU.getIMUHeading() - 360), 180) : IMU.getIMUHeading();
    correction = goalVisible ? -goalTrackDefendPID.update(angleMap(correction + goalAngle, 180), 0) : -headingPID.update(angleMap(correction, 180), 0);
    lrfValue = lrf.getDistance();
    if(goalVisible) {
        if(abs(correction + goalAngle) > 150) {
            if(lrfValue < DEFEND_BLOCK_DISTANCE) {
                lrfValue = DEFEND_GOAL_DISTANCE;
            }
        }
    }
    calculateDefenseMovement();
    calculateOutAvoidance(finalMovement);
    motors.updateDirection(finalMovement.direction, correction, finalMovement.speed);
}

void move() {
    if(attacking) {
        calculateAttack();
    } else {
        calculateDefense();
    }
}

// void decideRole() {
//     if(isConnected) {
//         if(!attacking) {
//             if(angleIsInside(270, 90, bluetooth.otherData.ballDir)) {
//                 if(tsops.getAvgStr() > bluetooth.otherData.ballStr) {
//                     if(switchTimer.timeHasPassed()) {
//                         attacking = true;
//                         LEDTimer.updateTimerDuration(LED_BLINK_TIME_ATTACK);
//                     }
//                 }
//             }
//         } else if(bluetooth.otherData.role) {
//             if(switchTimer.timeHasPassed()) {
//                 attacking = false;
//                 LEDTimer.updateTimerDuration(LED_BLINK_TIME_DEFEND);
//             }
//         }
//     } else {
//         attacking = false;
//     }
// }

void setup() {
    pinMode(LED_PIN, OUTPUT);
    digitalWrite(LED_PIN, HIGH);
    Serial.begin(9600);
    // delay(3000);
    initWire();
    IMU.IMUSetup();
    IMU.calibrate();
    IMU.findDrift();
    tsops.tsopsSetup();
    lights.lightSensorsSetup();
    IMU.driftPrevious = millis();
    motors.motorsSetup();
    motors.brake();
    pixy.init();
    #if !DEFAULT_ROLE
        lrf.begin();
        lrf.setDistanceMode(2);
    #endif
    digitalWrite(LED_PIN, LOW);
}

void loop() {
    Serial.println(0);
    tsops.read();
    Serial.println(1);
    lights.updateLineLocation();
    Serial.println(2);
    IMU.updateGyro();
    Serial.println(3);
    // decideRole();
    move();
    Serial.println(4);
    if(LEDTimer.timeHasPassed()) {
        digitalWrite(LED_PIN, ledOn);
        ledOn = !ledOn;
    }
    // BluetoothData sendData = {tsops.getBallDir(), tsops.getAvgStr(), attacking};
    // bluetooth.update(sendData);
}

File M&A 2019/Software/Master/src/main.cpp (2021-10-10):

#include <MPU.h>
#include <Camera.h>
#include <LSMultiplexer.h>
#include <MotorControllers.h>
#include <PID.h>

MPU imu;
Camera camera;
LSMultiplexer lightSensors;
MotorControllers motors;
PID distancePID(DISTANCE_KP, DISTANCE_KI, DISTANCE_KD, DISTANCE_MAX_SPEED);
PID centreDistancePID(CENTRE_DISTANCE_KP, CENTRE_DISTANCE_KI, CENTRE_DISTANCE_KD, CENTRE_DISTANCE_MAX_SPEED);
PID sidewaysPID(SIDEWAYS_KP, SIDEWAYS_KI, SIDEWAYS_KD, SIDEWAYS_MAX_SPEED);
PID centreSidewaysPID(CENTRE_SIDEWAYS_KP, CENTRE_SIDEWAYS_KI, CENTRE_SIDEWAYS_KD, CENTRE_SIDEWAYS_MAX_SPEED);
PID headingPID(HEADING_KP, HEADING_KI, HEADING_KD, HEADING_MAX_CORRECTION);
PID attackGoalTrackPID(ATTACK_GOAL_TRACK_KP, ATTACK_GOAL_TRACK_KI, ATTACK_GOAL_TRACK_KD, ATTACK_GOAL_TRACK_MAX_CORRECTION);
PID defendGoalTrackPID(DEFEND_GOAL_TRACK_KP, DEFEND_GOAL_TRACK_KI, DEFEND_GOAL_TRACK_KD, DEFEND_GOAL_TRACK_MAX_CORRECTION);

Movement calculateMove(float vertical, float horizontal) {
    Movement sendVal;
    sendVal.direction = floatMod(RADIANS_TO_DEGREES * atan2f(horizontal, vertical), 360);
    if(camera.robot.exists() && camera.ball.exists()) {
        Vect goal = Vect(DEFEND_X, DEFEND_Y, false) - camera.robot;
        float diff = floatMod(450 - imu.heading, 360.0) - floatMod(goal.arg + 180, 360.0);
        if(diff > 180) {
            diff -= 360;
        } else if(diff < -180) {
            diff += 360;
        }
        // correction = defendTrack.update(diff, 0);
        // Vect goal = Vect(DEFEND_X, DEFEND_Y, false) - camera.robot;
        sendVal.correction = -defendGoalTrackPID.update(diff, 0);
        // sendVal.correction = -defendGoalTrackPID.update(camera.defendingGoalAngle, 180);
    } else {
        sendVal.correction = headingPID.update((imu.heading > 180 ? imu.heading - 360 : imu.heading), 0);
    }
    sendVal.speed = sqrtf(vertical * vertical + horizontal * horizontal);
    return sendVal;
}

Movement calculateAttackMovement() {
    Movement sendVal;
    if(camera.ball.exists()) {
        float dir = camera.ball.arg > 270 ? camera.ball.arg - 450 : camera.ball.arg - 90;
        float ballAngleDifference = findSign(dir) * fmin(90, 0.04 * expf(0.15 * abs(dir)));
        float distMulti = max(0, -0.04 * camera.ball.mag + 2);
        float angleAdd = distMulti * ballAngleDifference;
        sendVal.direction = floatMod(450 - camera.ball.arg - angleAdd, 360.0);
        sendVal.correction = headingPID.update((imu.heading > 180 ? imu.heading - 360 : imu.heading), 0);
        if(camera.ball.mag < 30 && angleIsInside(70, 110, camera.ball.arg)) {
            sendVal.speed = ORBIT_FAST_SPEED;
        } else {
            sendVal.speed = ORBIT_SLOW_SPEED + (ORBIT_MEDIUM_SPEED - ORBIT_SLOW_SPEED) * (1.0 - abs(angleAdd) / 90.0);
        }
        return sendVal;
    // } else if(camera.robot.exists) {
    //     return calculateMove(centreDistancePID.update(-40 - cam.robot.jcamera.defendingGoalDistance, ATTACK_IDLE_DISTANCE), 0);
    }
    return calculateMove(0, 0);
}

Movement calculateDefenseMovement() {
    if(camera.ball.exists()) {
    //     if(camera.ball.mag < 30) {
    //         if(angleIsInside(70, 110, camera.ball.arg)) {
    //             if(camera.robot.exists() && camera.robot.j < -30) {
    //                 // return calculateAttackMovement();
    //             }
    //         }
    //     }
        if(angleIsInside(0, 180, camera.ball.arg)) {
            Vect temp = Vect(DEFEND_X, DEFEND_Y, false) - camera.robot;
            // float distance = camera.robot.exists() ? -60 - camera.robot.j : 0;
            return calculateMove(centreDistancePID.update(temp.mag, 40), sidewaysPID.update(90 - camera.ball.arg, 0));
        }
    //     return calculateAttackMovement();
    } else if(camera.robot.exists()) {
        Vect temp = Vect(DEFEND_X, DEFEND_Y, false) - camera.robot;
        return calculateMove(centreDistancePID.update(temp.mag, 40), -camera.robot.i);
    }
    return calculateMove(0, 0);
}

void setup() {
    delay(500);
    imu.init();
    camera.init();
    lightSensors.init();
    motors.init();
}

void loop() {
    imu.update();
    camera.update(imu.heading, true);
    lightSensors.update(imu.heading);
    Movement finalMovement = lightSensors.calculateOutAvoidance(imu.heading, calculateDefenseMovement());
    motors.update(finalMovement);
}

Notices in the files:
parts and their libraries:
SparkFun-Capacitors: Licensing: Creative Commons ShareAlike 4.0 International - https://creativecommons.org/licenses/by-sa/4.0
